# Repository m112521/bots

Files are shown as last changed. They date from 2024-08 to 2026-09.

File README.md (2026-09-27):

# BOTS

[Инструкция .PDF](https://drive.google.com/file/d/1NVx_HqoQqec8NSSLov3LOcF6pv9YKxNa/view?usp=sharing) 

[Схема .PDF](https://github.com/m112521/bots/blob/esp32-tb6612/ESP32TB6612_SVG_MOSFET/CAD/BOTS_PCB_2/BOTS_PCB_schematics.pdf)

[Исходный код](https://github.com/m112521/bots/blob/esp32-tb6612/src/web/DiffrentialControl_invert.ino) 

[BOM](https://docs.google.com/spreadsheets/d/1dyzHaP3tl7uu9WDstYaMej6k_q5ZT6EIcCH9GYrkqhs/edit?usp=sharing)

Slice 2

Slice 2 (1)

Slice 2 (2)

Slice 2 (3)

Slice 2 (4)

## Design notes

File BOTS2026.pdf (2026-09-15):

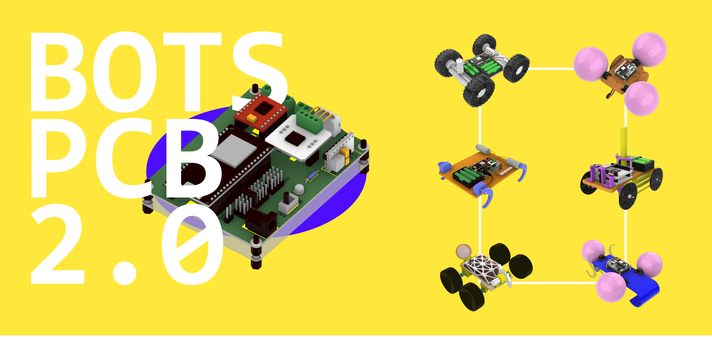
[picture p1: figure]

11 | 10 | 2 | 12
3

## 1 Плата

Набор на одну команду включает в себя:

Компоненты

1 | ESP32-WROOM 38 pin (+USB Micro)
2 | MD1 Драйвер для двух моторов TB6612
3 | T1 Силовой ключ (MOSFET) (https://amperka.ru/product/troyka-mosfet-n-channel-v3) [PIN 15]
4 | DC1 Понижающий преобразователь питания (https://amperka.ru/product/voltage-regulator-dc-dc-arduino)
5 | R1 Резистор
6 | LED1 Светодиод
7 | D1 Диод Шоттки 1N5822
8 | S1 Ползунковый переключатель
9 | P1 Гнездо питания
10 | D2 Диод 1N4001
11 | Гнездо штыревое мама
12 | M1 M2 M3 Клеммник винтовой

7

1

4

5

6

8

9

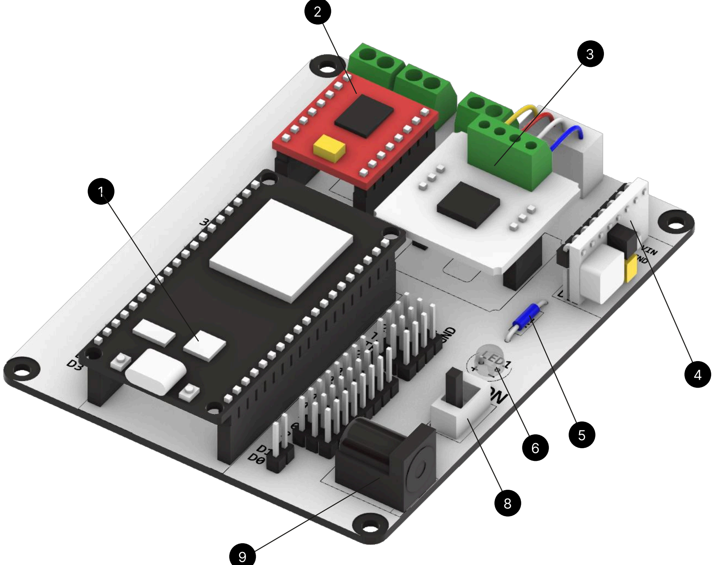
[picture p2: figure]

2 | Схема подключения питания и моторов
13 | DC-мотор 12В с редуктором (https://compacttool.ru/motor-s-reduktorom-jga25-370-12v-sootnoshenie-134-205-obmin)
14 | Держатель для 3 аккумуляторов
15 | Аккумулятор Li-ion 18650

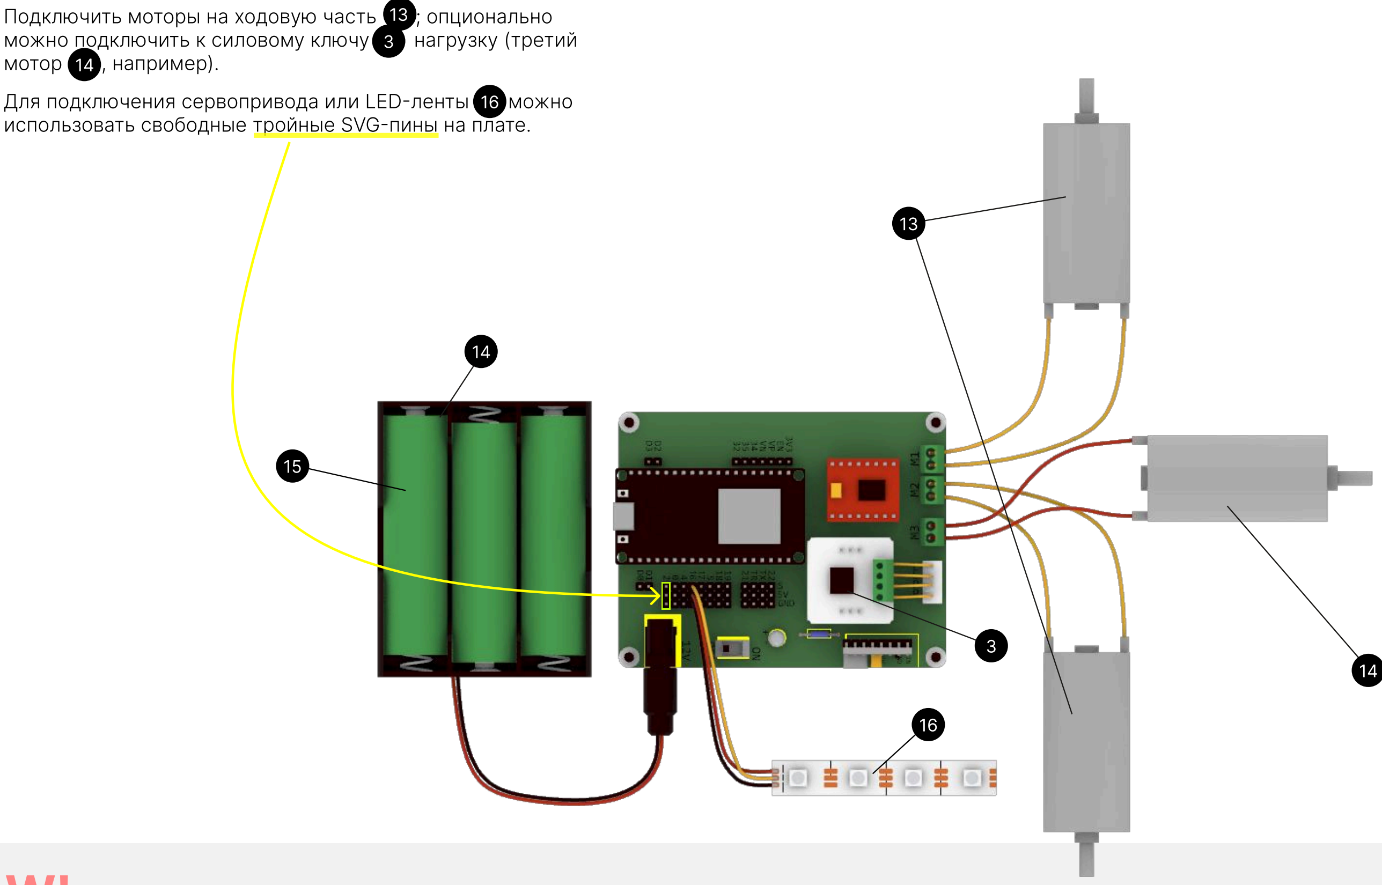
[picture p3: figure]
Подключить моторы на ходовую часть; ; опционально; можно подключить к силовому ключу; нагрузку (третий; мотор; , например).; Для подключения сервопривода или LED-ленты; можно

использовать свободные тройные SVG-пины на плате.

W! Держите заряд всех аккумуляторов выше 3.7 В

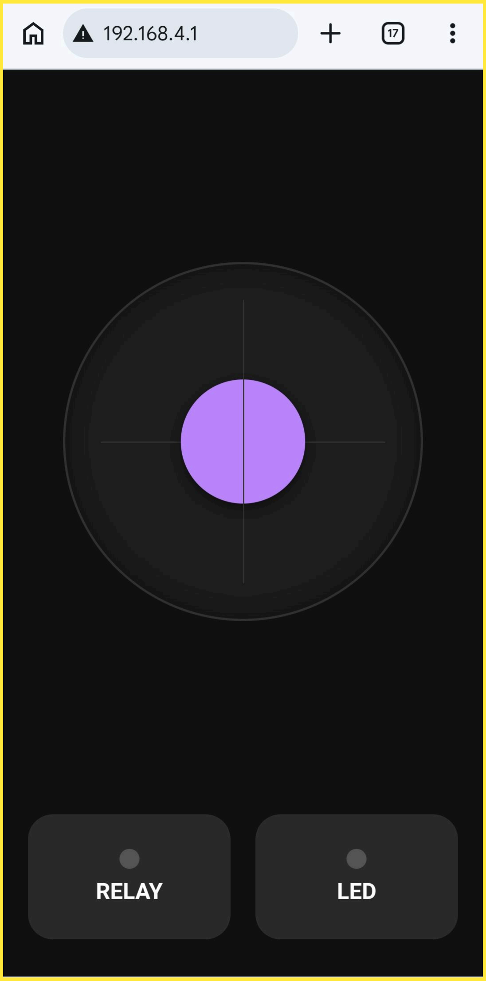
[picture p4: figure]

## 3 Управление роботом

Для управления роботом используйте смартфон:

Подключитесь к WiFi сети с именем botN (где N - номер, указанный на плате) и ввести пароль 12345678.
Откройте браузер и введите IP-адрес 192.168.4.1 в адресную строку.
Используйте джойстик для управления навпралением и скоростью движения робота.
Кнопка RELAY подает напряжение на нагрузку MOSFETа (PIN15), подключенную к клеммнику М3.

Исходный код (https://github.com/m112521/bots/blob/esp32-tb6612/src/web/DifferentialControl_AP)

## 4 Программирование (для желающих использовать свой код)

Для программирования управляющей платы понадобится скачать и установить Arduino Studio. (https://www.arduino.cc/en/software)

После запуска Arduino Studio необходимо установить дополнительные компоненты (библиотеки, плагины):

В Arduino Studio перейти в File -> Preferences. Скопировать и вставить строку ниже в поле Additional boards manager URLs (если в поле уже присутсвуют ссылки, то нужно поставить запятаю в конце строки и вставить новую ссылку):

https://espressif.github.io/arduino-esp32/package_esp32_index.json

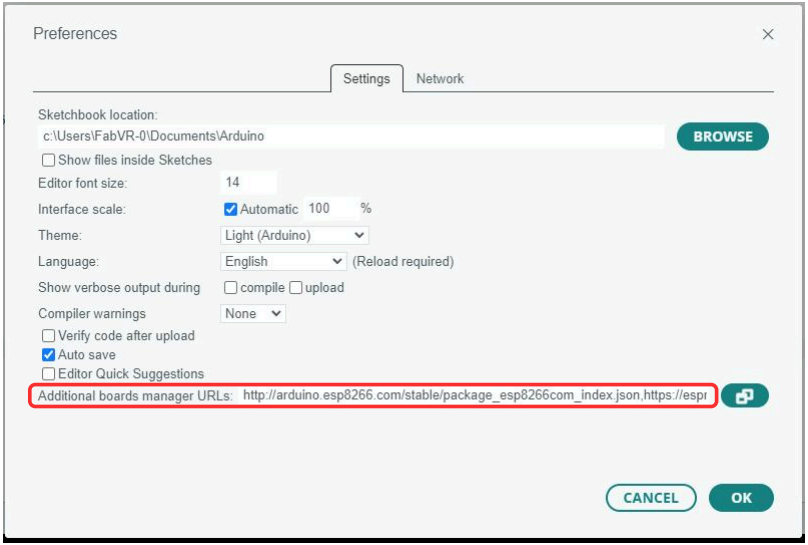
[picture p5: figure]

В Arduino Studio перейти в Boards Manager, ввести в строке поиска ESP32, найти в найденном списке esp32 by Espressif Systems , выбрать версию 2.0.15 и нажать на кнопку INSTALL : ³

1 | 2

2

2
1

3

Скачать, распаковать и установить драйвер (от имени Администратора) USB-UART CP210x_VCP_Windows.zip. (https://github.com/m112521/bots/blob/esp32-tb6612/libs/CP210x_VCP_Windows.zip)

Скачать библиотеки ниже (без раcпаковки !), перейти в Arduino Studio: Sketch -> Include Library -> Add .ZIP Library... и последовательно выбрать все скаченные архивы:

Перейти в Arduino Studio в Library Manager, ввести в поиске Arduino_JSON, найти в списке Arduino_JSON by Arduino,

выбрать версию 0.1.0 и нажать на кнопку INSTALL :

TB6612 (https://github.com/m112521/bots/blob/esp32-tb6612/libs/TB6612FNG_ESP32-master.zip)

AsyncTCP-master.zip (https://github.com/m112521/bots/blob/esp32-tb6612/libs/AsyncTCP-master.zip)

ESPAsyncWebServer-master.zi ESPAsyncWebServer-master.zi (https://github.com/m112521/bots/blob/esp32-tb6612/libs/ESPAsyncWebServer-master.zip)p (https://github.com/m112521/bots/blob/esp32-tb6612/libs/ESPAsyncWebServer-master.zip)

3

1 | 2

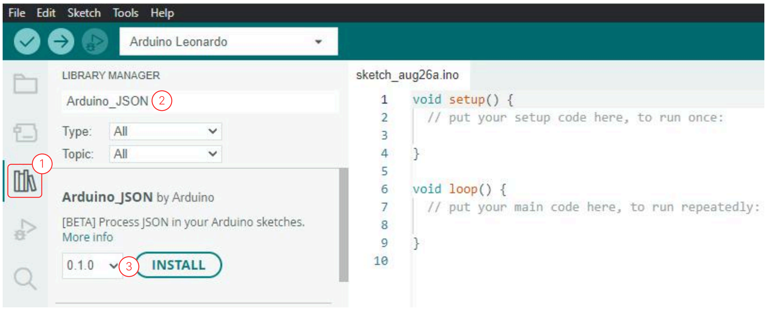
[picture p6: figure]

Перейти в Arduino Studio Library Manager, ввести в поиске AnalogWrite, найти в списке ESP32 ESP32S2 AnalogWrite by
David Lloyd, выбрать версию 5.0.1 и нажать на кнопку INSTALL : 3

1

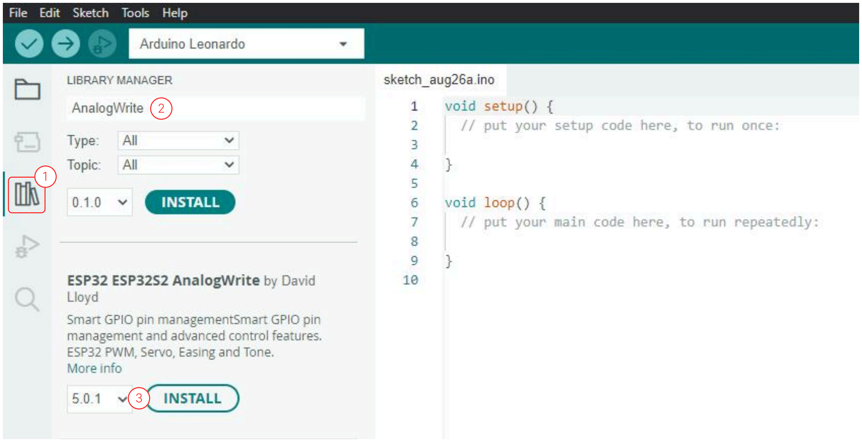
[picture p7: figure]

З агрузка новой программы. Этот пункт необходимо повторять при каждом внесении изменений в код программы:

Подключить плату ESP32 к компьютеру с помощью провода USB.

Нажать на выпающий список и выбрать USB-порт, к которому подключена управляющая плата: 1

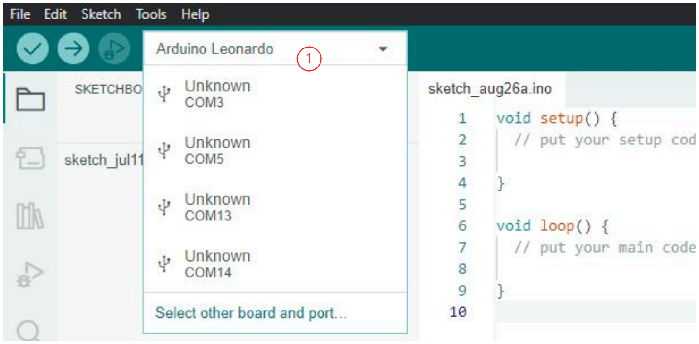
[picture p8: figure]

В строке поиска открывшегося окна ввести ESP32, выбрать из списка ESP32 Dev Module и нажать на кнопку
OK:
1 | 2

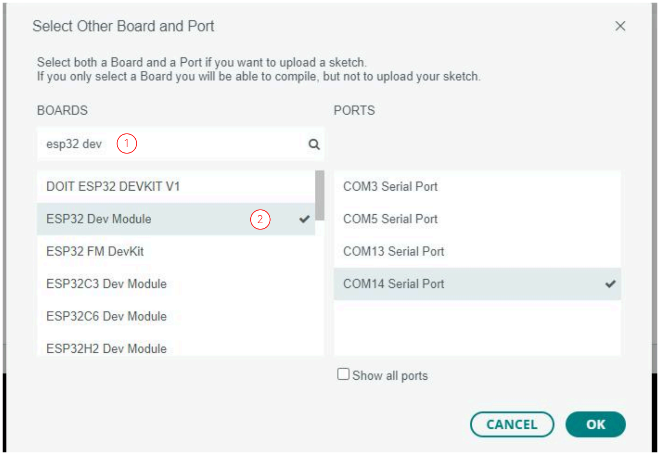
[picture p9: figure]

У бедитесь, что в поле выпадающего списка указано ESP32 Dev Module. После нажмите на кнопку | для
загрузки программы на микроконтроллер:
1 | 2
2 | 1

Во врямя загрузки программы (до появления сообщения об успешной загрузке в Arduino Studio) необходимо удерживать кнопку BOOT на управляющей плате: ¹

После успешной загрузки кода необходимо перезагрузить плату, нажав на кнопку RST.

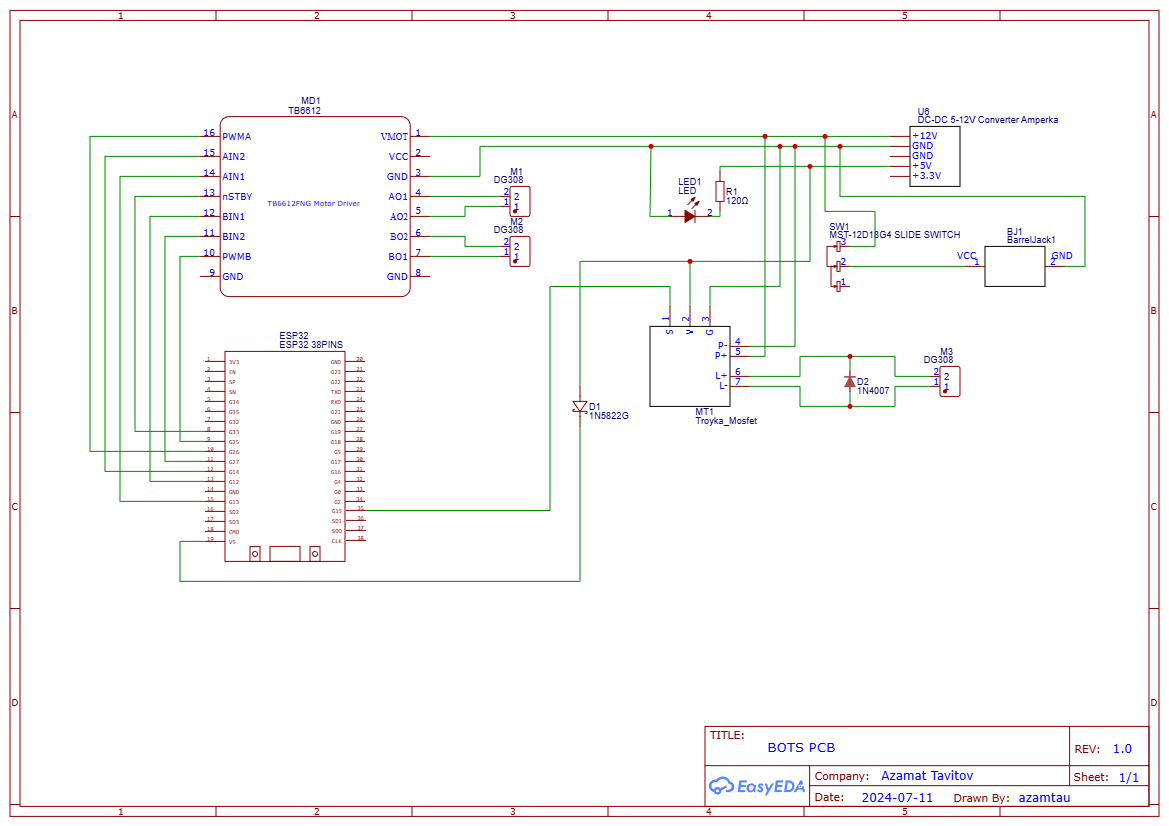
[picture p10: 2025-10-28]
ESP32TB6612_SVG_MOSFET/CAD/BOTS_PCB_2/Schematic_tb6612esp32_2025-10-28.png

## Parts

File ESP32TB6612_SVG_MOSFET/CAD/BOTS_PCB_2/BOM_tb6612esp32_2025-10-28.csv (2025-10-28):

ID | Name | Designator | Footprint | Quantity | Manufacturer Part | Manufacturer | Supplier | Supplier Part | Price | Pins
1 | BarrelJack1 | BJ1 | BARRELJACKFC681478 | 1 |  |  |  |  |  | 2
2 | 1N5822G | D1 | DO-201AD_BD5.1-L8.4-P12.50-D1.3-FD-1 | 1 | 1N5822G | onsemi(安森美) | LCSC | C59208 | 0.589 | 2
3 | 1N4007 | D2 | 1N4007 | 1 |  |  |  |  |  | 2
4 | ESP32 38PINS | ESP32 | ESP32 38PINS | 1 |  |  |  |  |  | 38
5 | LED | LED1 | LED-TH_LED-DP2-2LED-AMCC | 1 | 5600 | VccLite | Digi-Key | L20325-ND |  | 2
6 | DG308 | M1,M2,M3 | CONN-TH_DG308-2.54-02P-14-00A | 3 | DG308-2.54-02P-14-00A(H) | DEGSON（高正/高松） | LCSC | C699496 | 0.312 | 2
7 | TB6612 | MD1 | TB6612FNG | 1 |  |  |  |  |  | 16
8 | Troyka_Mosfet | MT1 | TROYKA MOSFET | 1 |  | Amperka |  |  |  | 7
9 | 120Ω | R1 | RES-TH_BD2.3-L6.5-P10.50-D0.5 | 1 | CF1/4W-110KΩ±5% T52 | CCO(千志电子) | LCSC | C120104 | 0.006 | 2
10 | MST-12D18G4 SLIDE SWITCH | SW1 | SW-SMD_MST-12D18G4-SPDT-SLIDE-SWITCH | 1 | MST-12D18G4 SPDT Slide Switch | SHOU HAN(首韩) | LCSC | C49023767 | 0.075 | 3
11 | DC-DC 5-12V Converter Amperka | U6 | DC-DC 5-12V CONVERTER AMPERKA | 1 | DC-DC Converter |  |  |  |  | 5

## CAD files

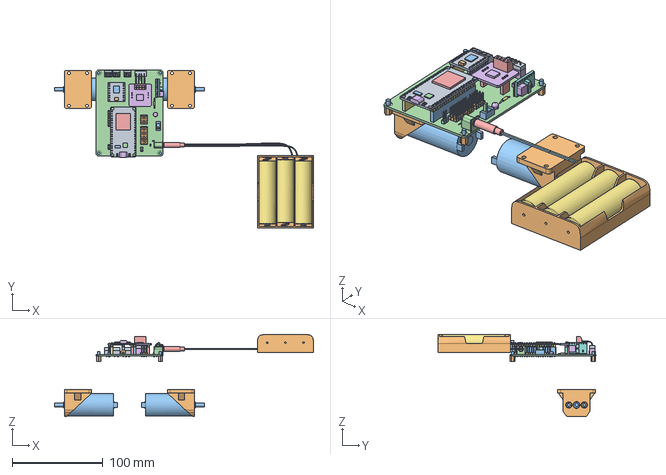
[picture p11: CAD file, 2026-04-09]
Electronics_Assembly_PCB2.stp
286.2 x 174.5 x 91.1 mm

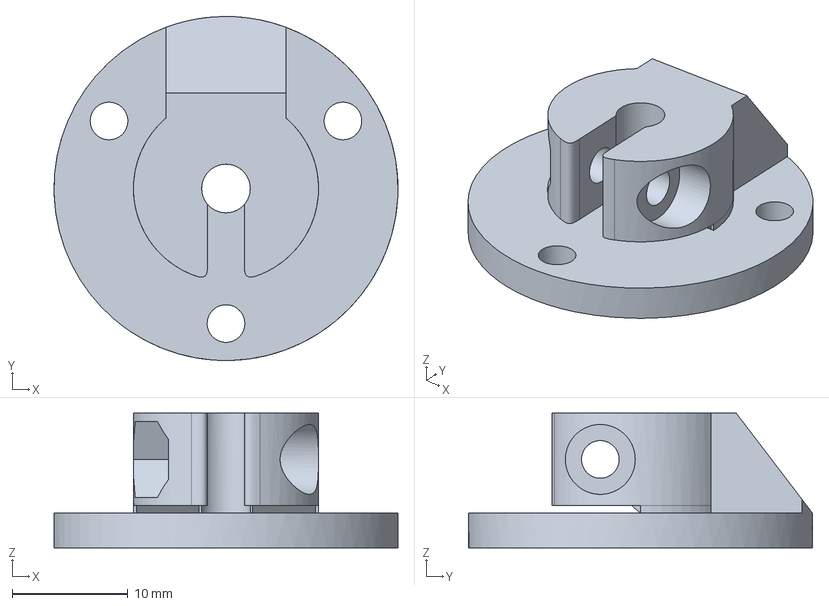
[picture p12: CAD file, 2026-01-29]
BOTS_BOX/onShaftHolder.stp
29.7 x 29.7 x 11.6 mm

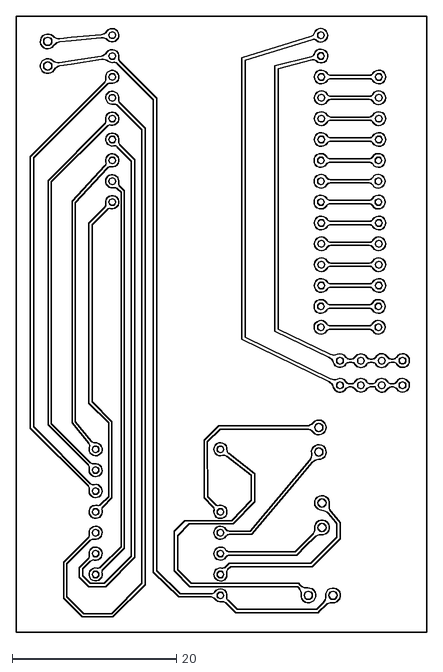
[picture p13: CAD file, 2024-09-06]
ESP32TB6612_SVG/ESP8266TB6612_SVG_ENC_SeparatedPower.dxf
50.0 x 75.0

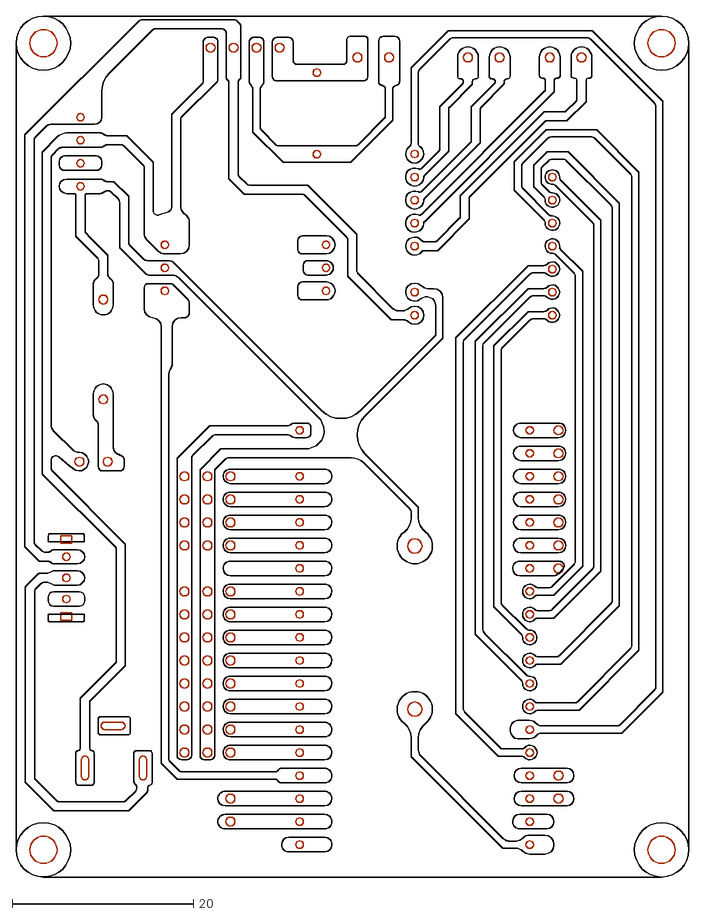
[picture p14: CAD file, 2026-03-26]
ESP32TB6612_SVG_MOSFET/CAD/BOTS_PCB_2/BOTS_PCB_2.2_TRACES_MIRROR.dxf
74.2 x 95.0

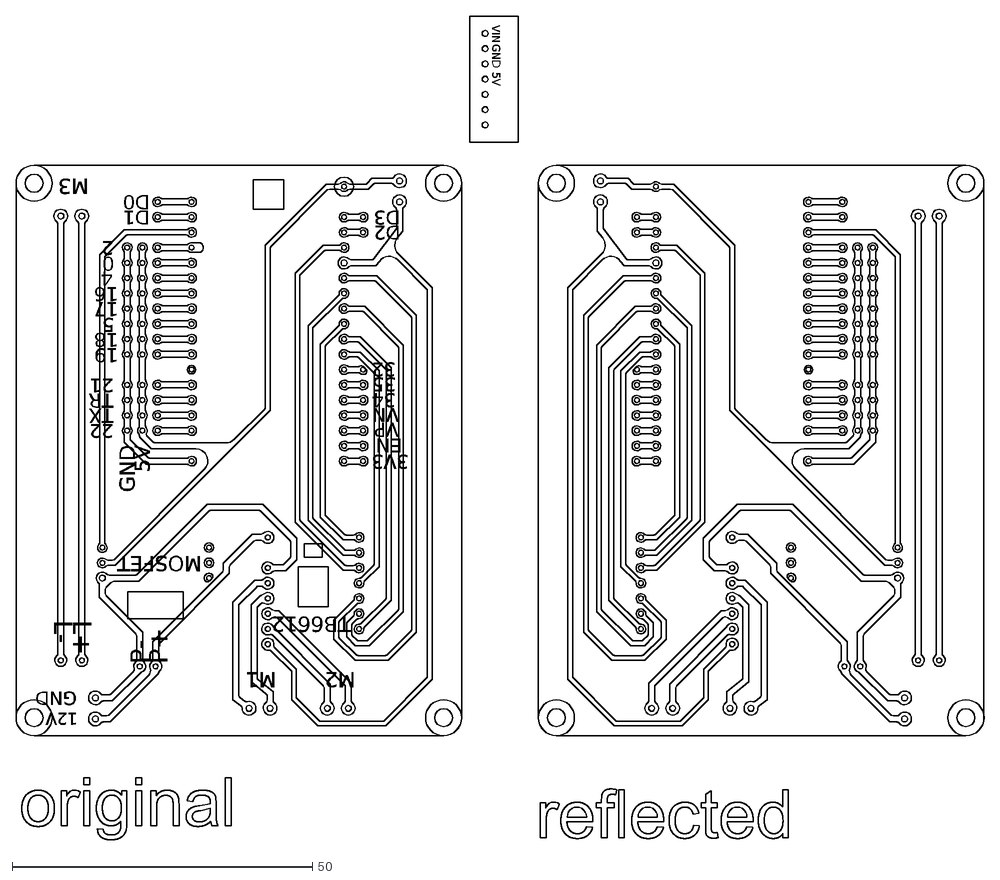
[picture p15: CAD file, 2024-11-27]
ESP32TB6612_SVG_MOSFET/CAD/ESP32TB6612_MOSFET_vector.dxf
5V
GND
VIN
P-
12V
L-
L+
P+
MOSFET
D2
D3
D0
D1
19
18
5
17
2
4
16
0
21
TR
TX
22
32
35
34
VN
VP
EN
3V3
TB6612
M3
M1
M2

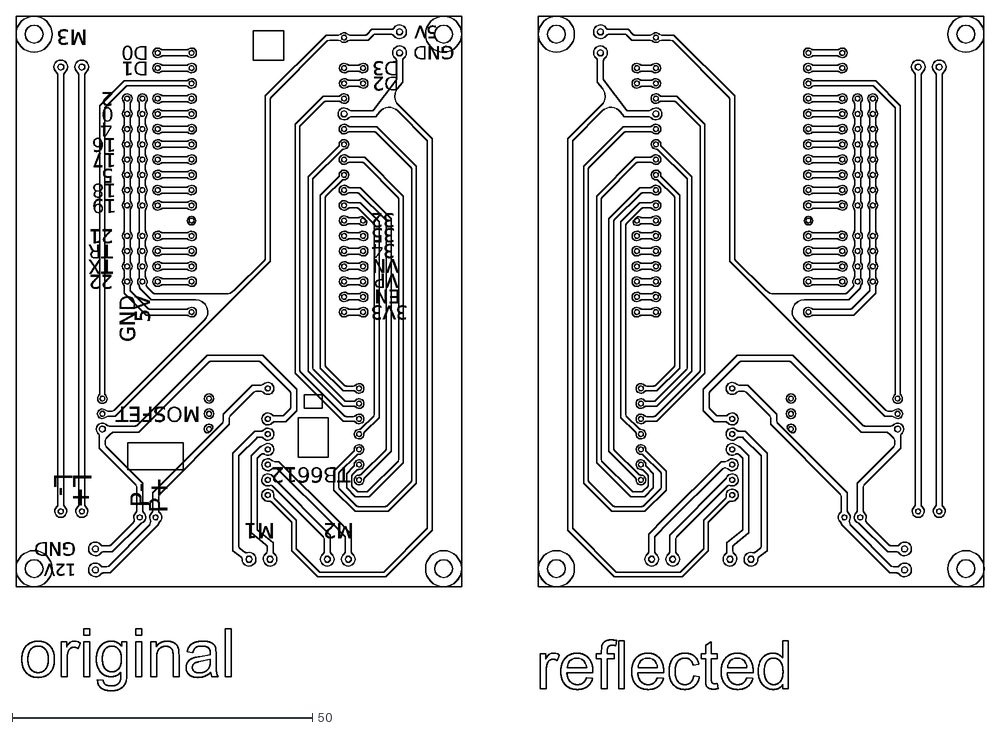
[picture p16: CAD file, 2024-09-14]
ESP32TB6612_SVG_MOSFET/CAM/250x150/ESP32TB6612_MOSFET_vector.dxf
5V
M2
M1
M3
GND
TB6612
3V3
EN
VP
VN
34
35
32
22
TX
TR
21
0
16
4
2
17
5
18
19
D1
D0
D3
D2
MOSFET
P+
P-
L+
L-
12V

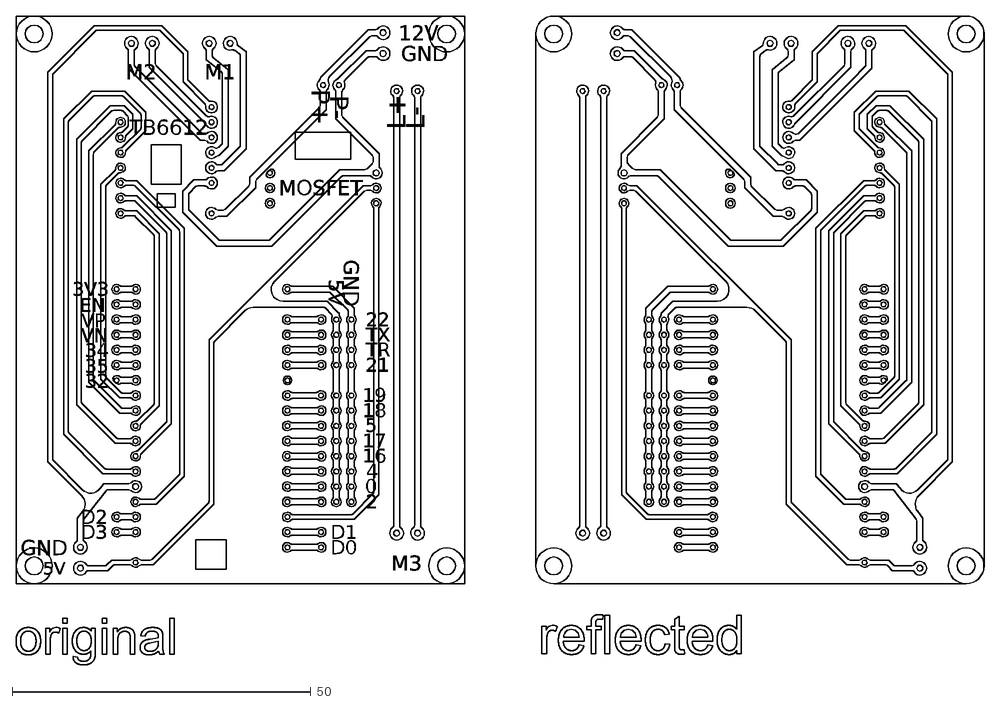
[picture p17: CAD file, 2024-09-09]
ESP32TB6612_SVG_MOSFET/CAM/ESP32TB6612_MOSFET_vector.dxf
L-
L+
P-
P+
MOSFET
D2
D3
D0
D1
19
18
5
17
2
4
16
0
21
TR
TX
22
32
35
34
VN
VP
EN
3V3
5V
TB6612
GND
M3
M1
M2
12V

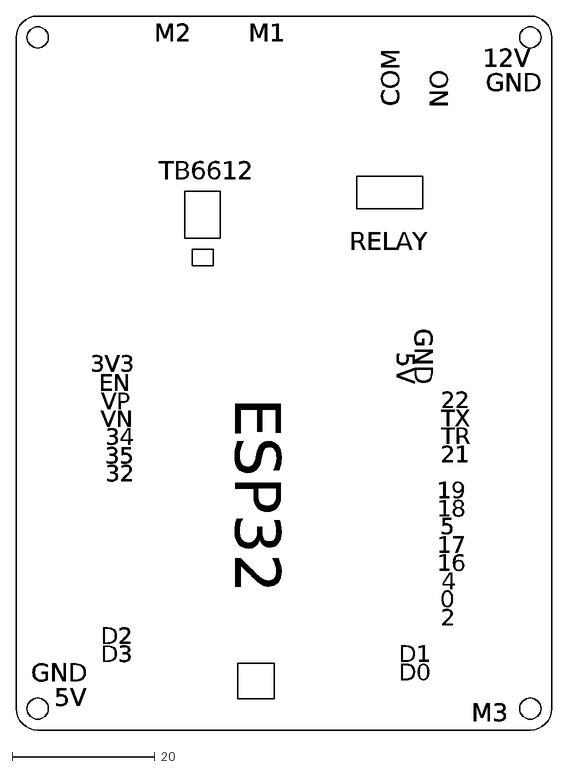
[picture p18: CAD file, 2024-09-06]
ESP32TB6612_SVG_RELAY/CAD/SilkBOTS-Shield.dxf
ESP32
GND
12V
D2
D3
D0
D1
19
18
5
17
2
4
16
0
21
TR
TX
22
32
35
34
VN
VP
EN
3V3
5V
M2
M1
M3
TB6612
RELAY
COM
NO

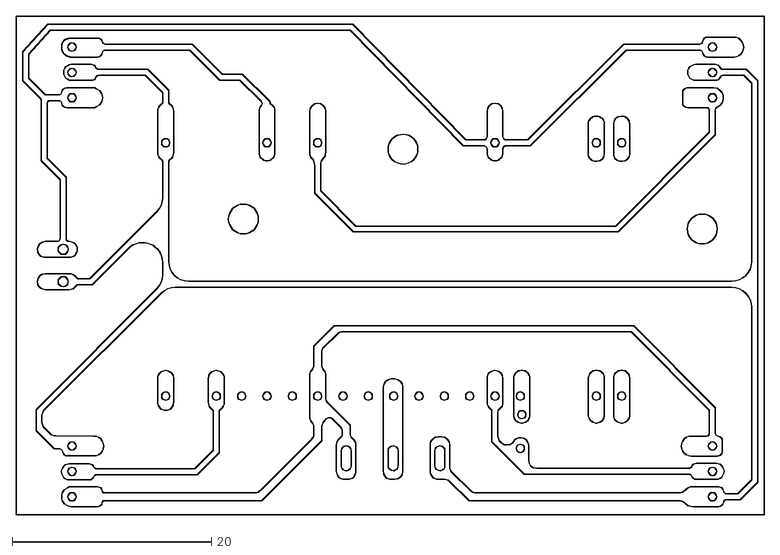
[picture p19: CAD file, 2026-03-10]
ESPNOW_JOYSTICK/CAD/minibot_traces_R12Lines.dxf
75.0 x 50.0

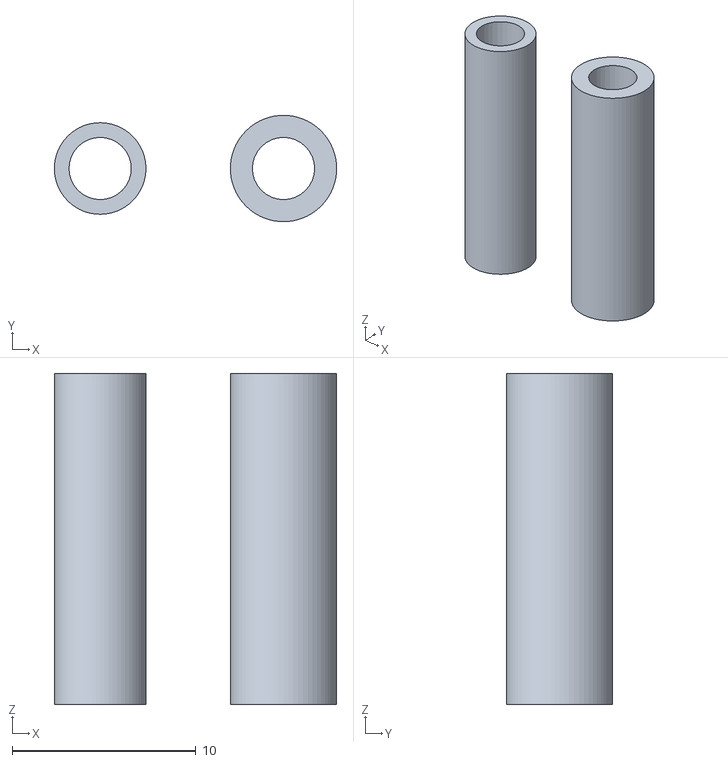
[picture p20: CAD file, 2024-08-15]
ESPNOW_JOYSTICK/STL/spacersJoystick.stl
15.4 x 5.78 x 18.0

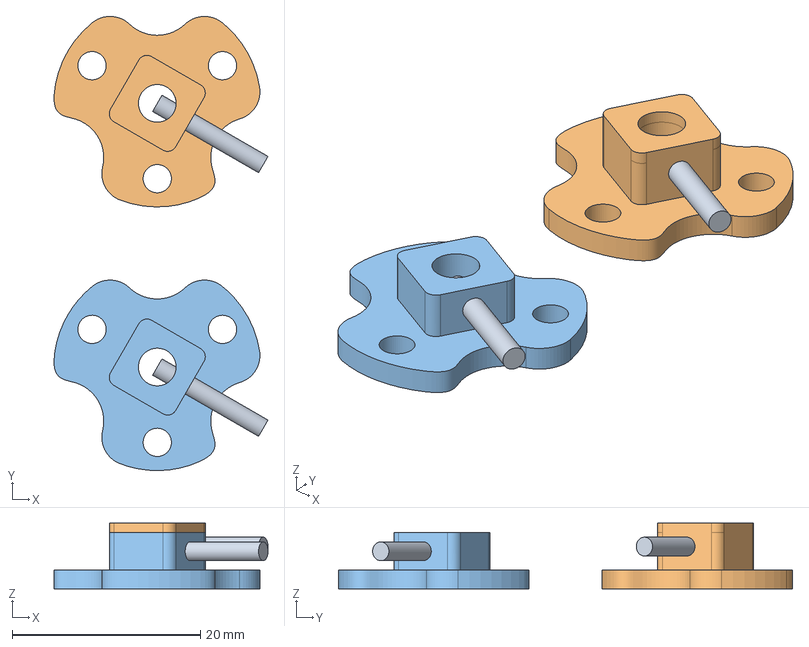
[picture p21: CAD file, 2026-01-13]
BOTS_BOX/onShaftHolder_cnc.stp
22.7 x 48.2 x 7.00 mm

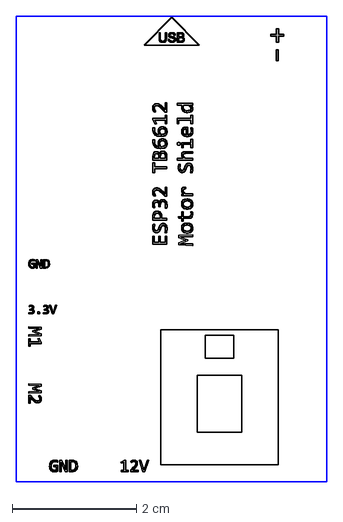
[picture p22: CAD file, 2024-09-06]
ESP32TB6612_SVG/ESP8266TB6612_SVG_ENC_SeparatedPower_silk.dxf
5.00 x 7.50 cm

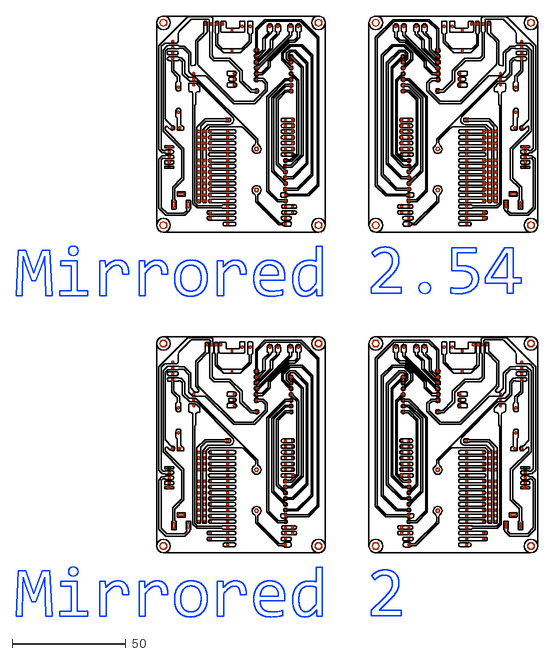
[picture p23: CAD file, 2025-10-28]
ESP32TB6612_SVG_MOSFET/CAD/BOTS_PCB_2/BOTS_PCB_2.0_TRACES_HOLES.dxf
229.3 x 264.2

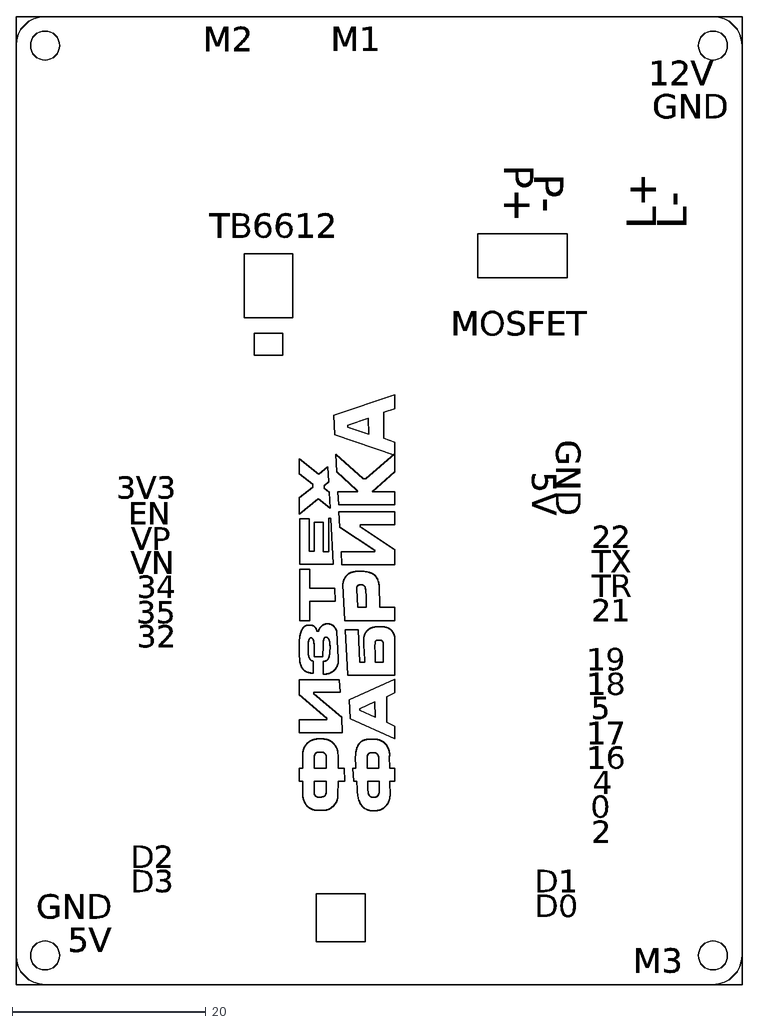
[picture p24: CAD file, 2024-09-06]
ESP32TB6612_SVG_MOSFET/CAD/ESP32TB6612_MOSFET_SILK_FF.dxf
GND
TB6612
5V
M3
M1
M2
3V3
EN
VP
VN
34
35
32
22
TX
TR
21
0
16
4
2
17
5
18
19
D1
D0
D3
D2
12V
MOSFET
P+
P-
L+
L-

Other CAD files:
ESPNOW_JOYSTICK/CAD/minibot_traces_R12Natural.dxf
BOTS_BOX/bots_cb_box.dxf
ESP32TB6612_SVG_MOSFET/CAD/BOTS_PCB_2/UVMaskForRhino.dxf
ESP32TB6612_SVG_MOSFET/CAD/ESP32TB6612_MOSFET_TRACES.dxf
BOTS_BOX/cap.stl
BOTS_BOX/cap_acrylic.dxf
BOTS_BOX/cap_aracal.dxf
BOTS_BOX/cap_graph.dxf
BOTS_BOX/clamp.stl
BOTS_BOX/holderFootprint.dxf
BOTS_BOX/level3.stl
BOTS_BOX/onoffFootprint.dxf
BOTS_BOX/shell.stl
ESP32TB6612_SVG/ESP32TB6612_SVG.3dm
ESP32TB6612_SVG_MOSFET/CAD/BOTS_PCB_2.0.3dm
ESP32TB6612_SVG_MOSFET/CAD/BOTS_PCB_2/BOTS2_Engraving.dxf
ESP32TB6612_SVG_MOSFET/CAD/BOTS_PCB_2/BOTS2_TracesOnly.dxf
ESP32TB6612_SVG_MOSFET/CAD/BOTS_PCB_2/BOTS_PCB_2.0_R7.3dm
ESP32TB6612_SVG_MOSFET/CAD/BOTS_PCB_2/BOTS_PCB_2_Mask.dxf
ESP32TB6612_SVG_MOSFET/CAD/BOTS_PCB_2/ServoShileld.dxf
ESP32TB6612_SVG_MOSFET/CAD/ESP32TB6612_MOSFET_SILK.dxf
ESP32TB6612_SVG_MOSFET/CAD/ESP32TB6612_MOSFET_TRACES_FF.dxf
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

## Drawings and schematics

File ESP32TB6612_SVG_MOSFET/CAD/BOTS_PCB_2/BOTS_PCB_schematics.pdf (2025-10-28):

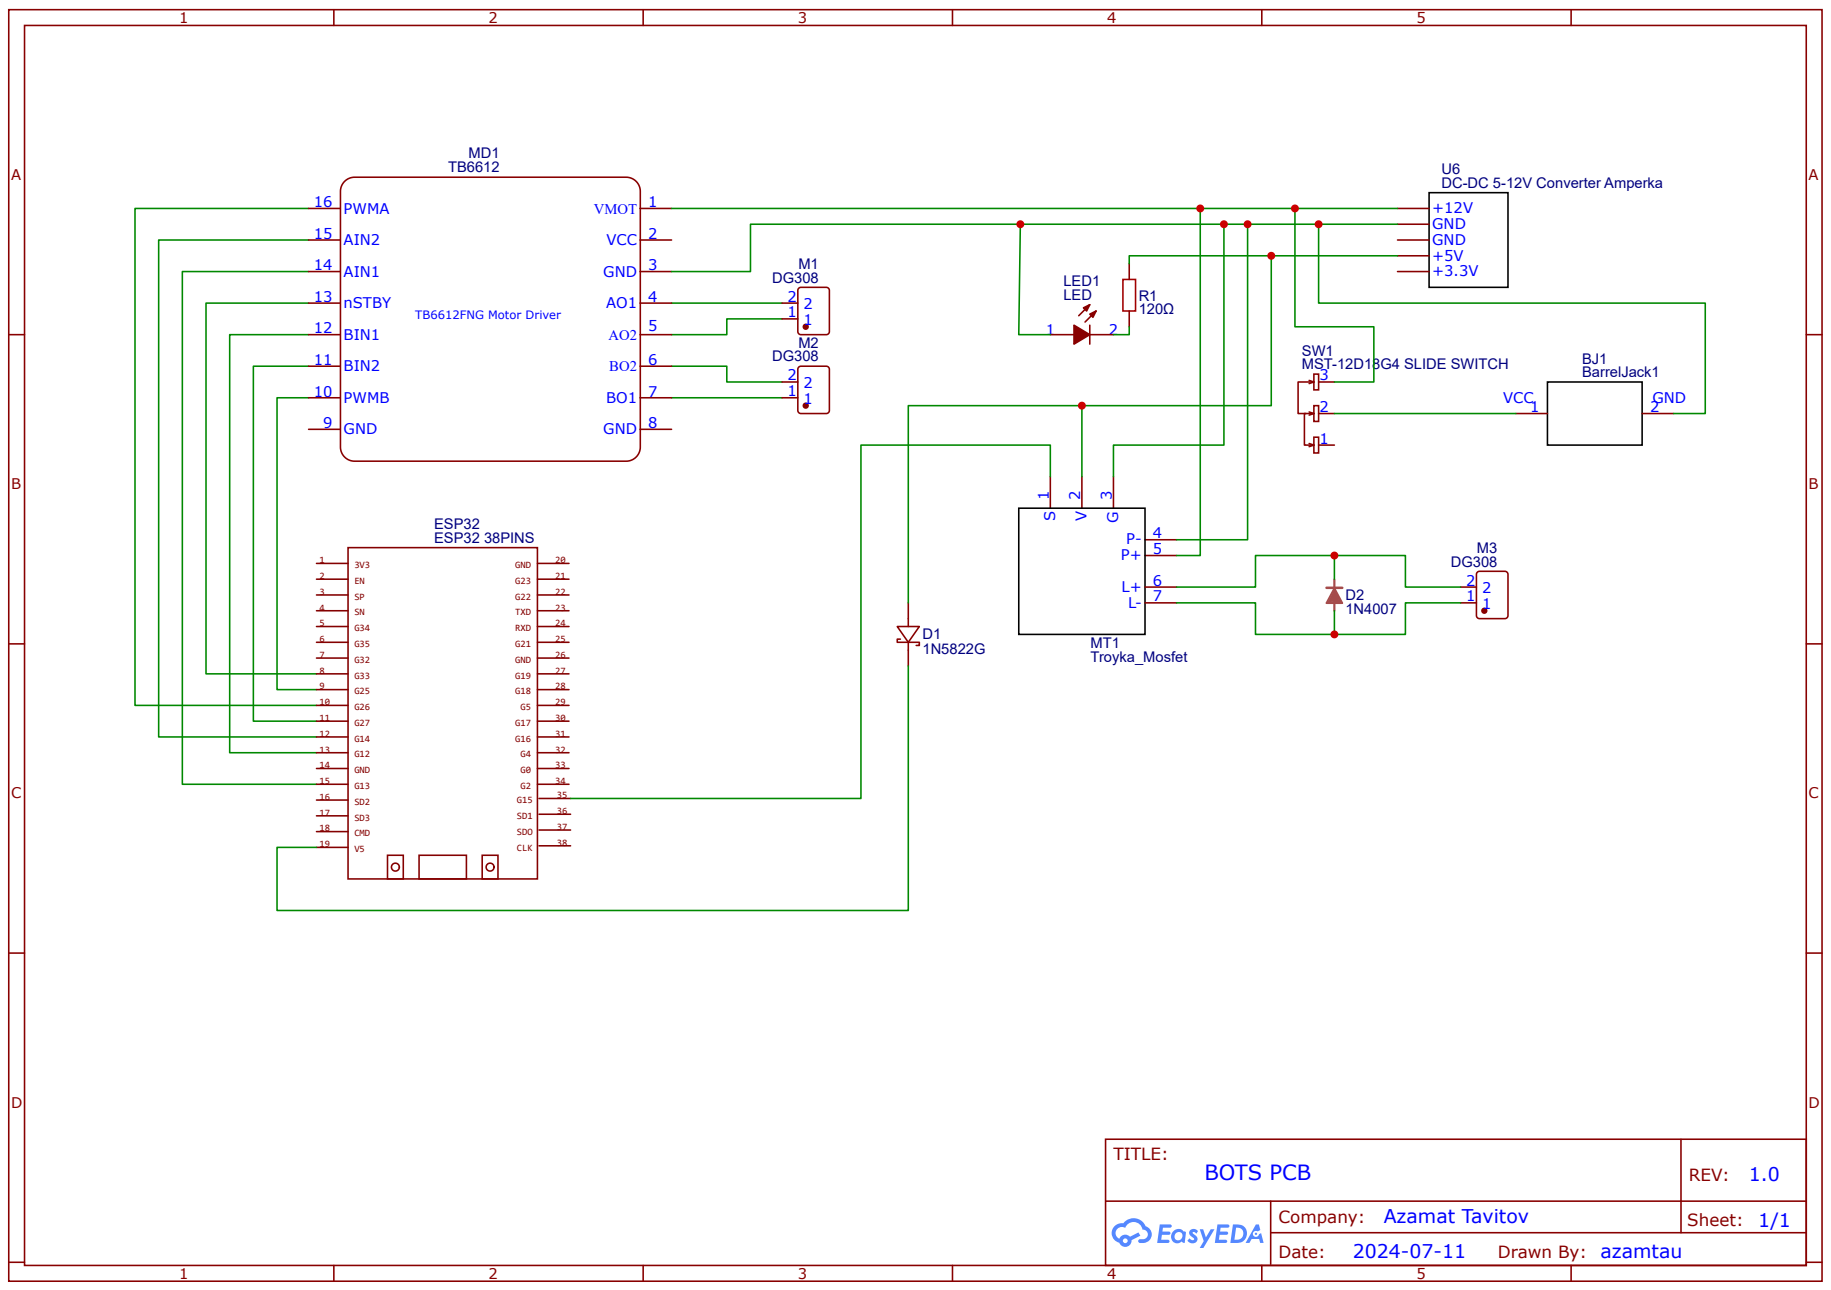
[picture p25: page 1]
TITLE:; BOTS PCB; REV: 1.0; Date:; Sheet: 1/1; VMOT 1; VCC; GND; 8 GND; PWMB 10; BIN2; BIN1; nSTBY 13; AIN1; AIN2; PWMA 16; TB6612FNG Motor Driver; ESP32 38PINS; ESP32; TXD; RXD; CLK; SDO; CMD; Troyka_Mosfet; DC-DC 5-12V Converter Amperka; MST-12D18G4 SLIDE SWITCH; BarrelJack1; VCC 1; GND 2; LED; LED1

Company: Azamat Tavitov

Drawn By: azamtau

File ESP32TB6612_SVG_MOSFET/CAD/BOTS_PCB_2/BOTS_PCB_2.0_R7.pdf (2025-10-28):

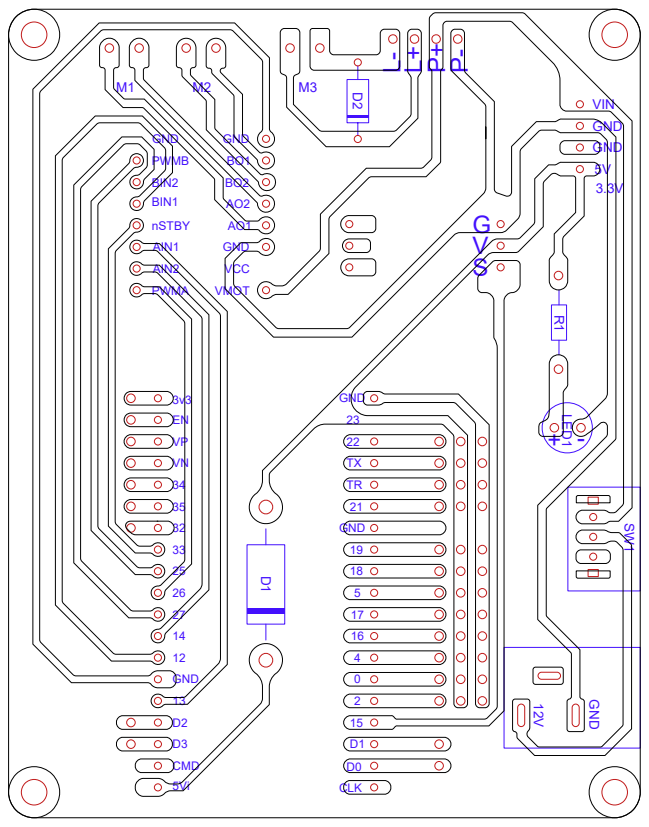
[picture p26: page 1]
GND; LED1; PWMA; CMD; VIN; BIN2; BIN1; nSTBY; AIN1; VCC; AIN2; CLK; PWMB

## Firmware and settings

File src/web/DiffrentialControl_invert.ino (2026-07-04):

#include <TB6612_ESP32.h>
#include <WiFi.h>
#include <AsyncTCP.h>
#include <ESPAsyncWebServer.h>
#include <Arduino_JSON.h>

#define AIN1 13
#define BIN1 12
#define AIN2 14
#define BIN2 27
#define PWMA 26
#define PWMB 25
#define STBY 33

const char* ssid = "bot1";
const char* password = "12345678";

#define RELAY_PIN 15
#define LED_PIN 2 

// Replaced 'direction' and 'speed' with X/Y coordinates
int joyX = 0; 
int joyY = 0;
int fire = 0;
int led = 0;

// Motor inversion states (1 = normal, -1 = inverted)
int invert1 = 1;
int invert2 = 1;

unsigned long lastCommandTime = 0; 
const long COMMAND_TIMEOUT = 3000; 

AsyncWebServer server(80);
AsyncWebSocket ws("/ws");

JSONVar readings;

const int offsetA = 1;
const int offsetB = 1;

Motor motor1 = Motor(AIN1, AIN2, PWMA, offsetA, STBY, 5000, 8, 1);
Motor motor2 = Motor(BIN1, BIN2, PWMB, offsetB, STBY, 5000, 8, 2);

const char index_html[] PROGMEM = R"rawliteral(
<!DOCTYPE html>
<html>
<head>
    <meta name="viewport" content="width=device-width, initial-scale=1.0, maximum-scale=1.0, user-scalable=no">
    <title>Bot Controller</title>
    <style>
        :root {
            --bg-color: #121212;
            --card-bg: #1e1e1e;
            --text-color: #ffffff;
            --btn-bg: #2c2c2c;
            --accent: #bb86fc;
            --fire-color: #cf6679;
            --led-color: #03dac6;
            --invert-color: #ffb74b; /* Orange for invert buttons */
        }

        * { box-sizing: border-box; margin: 0; padding: 0; }

        body {
            background-color: var(--bg-color);
            color: var(--text-color);
            font-family: -apple-system, BlinkMacSystemFont, "Segoe UI", Roboto, Helvetica, Arial, sans-serif;
            height: 100dvh;
            width: 100vw;
            overflow: hidden;
            display: flex;
            justify-content: center;
            align-items: center;
            -webkit-user-select: none;
            user-select: none;
            touch-action: none; 
        }

        .controller {
            display: flex;
            flex-direction: column;
            width: 100%;
            max-width: 500px;
            height: 100%;
            padding: 20px;
            gap: 20px;
        }

        /* --- JOYSTICK SECTION --- */
        .joystick-section {
            flex: 1; /* Takes up all remaining space */
            display: flex;
            justify-content: center;
            align-items: center;
            min-height: 0;
        }

        .joystick-zone {
            position: relative;
            width: min(75vw, 350px);
            aspect-ratio: 1 / 1; /* Perfect circle */
            max-height: 100%;
            background-color: var(--card-bg);
            border-radius: 50%;
            border: 2px solid #333;
            box-shadow: inset 0 0 20px rgba(0,0,0,0.5);
        }

        /* Crosshair in the center for visual reference */
        .joystick-zone::before, .joystick-zone::after {
            content: '';
            position: absolute;
            background: #333;
        }
        .joystick-zone::before { top: 50%; left: 10%; right: 10%; height: 1px; }
        .joystick-zone::after { left: 50%; top: 10%; bottom: 10%; width: 1px; }

        .joystick-knob {
            position: absolute;
            width: 35%;
            height: 35%;
            background-color: var(--accent);
            border-radius: 50%;
            top: 50%;
            left: 50%;
            transform: translate(-50%, -50%); /* Center it perfectly */
            box-shadow: 0 4px 10px rgba(0,0,0,0.5);
            pointer-events: none; /* Touches go to the zone, not the knob */
            transition: box-shadow 0.2s;
        }

        .joystick-knob.active {
            box-shadow: 0 0 20px var(--accent);
        }

        /* --- ACTION SECTION --- */
        .action-section {
            flex: 0 0 auto;
            display: grid;
            grid-template-columns: 1fr 1fr; /* 2x2 Grid layout */
            gap: 15px;
            padding-bottom: 10px;
        }

        .action-btn {
            width: 100%;
            aspect-ratio: 2.2 / 1; /* Wider buttons for the grid */
            max-height: 90px;
            background-color: var(--btn-bg);
            border: 3px solid transparent;
            border-radius: 20px;
            color: var(--text-color);
            font-size: 16px;
            font-weight: bold;
            display: flex;
            flex-direction: column;
            justify-content: center;
            align-items: center;
            gap: 6px;
            outline: none;
            -webkit-tap-highlight-color: transparent;
            transition: all 0.2s;
        }

        .indicator {
            width: 14px;
            height: 14px;
            border-radius: 50%;
            background-color: #555;
            transition: background-color 0.2s;
        }

        .fire-active { border-color: var(--fire-color); }
        .fire-active .indicator { background-color: var(--fire-color); box-shadow: 0 0 10px var(--fire-color); }

        .led-active { border-color: var(--led-color); }
        .led-active .indicator { background-color: var(--led-color); box-shadow: 0 0 10px var(--led-color); }

        .invert-active { border-color: var(--invert-color); }
        .invert-active .indicator { background-color: var(--invert-color); box-shadow: 0 0 10px var(--invert-color); }

    </style>
</head>
<body>

    <div class="controller">
        <!-- Joystick -->
        <div class="joystick-section">
            <div class="joystick-zone" id="joystick-zone">
                <div class="joystick-knob" id="joystick-knob"></div>
            </div>
        </div>

        <!-- Action Buttons (2x2 Grid) -->
        <div class="action-section">
            <button class="action-btn" id="btn-fire">
                <div class="indicator"></div>
                RELAY
            </button>
            <button class="action-btn" id="btn-led">
                <div class="indicator"></div>
                LED
            </button>
            <button class="action-btn" id="btn-invert1">
                <div class="indicator"></div>
                INVERT M1
            </button>
            <button class="action-btn" id="btn-invert2">
                <div class="indicator"></div>
                INVERT M2
            </button>
        </div>
    </div>

<script>
let gateway = `ws://${window.location.hostname}/ws`;
let websocket;

const zone = document.getElementById('joystick-zone');
const knob = document.getElementById('joystick-knob');
let isDragging = false;
let zoneRect, maxRadius;

window.addEventListener('load', onload);

function onload(event) {
    initWebSocket();
    initButtons();
    initJoystick();
}

function initJoystick() {
    // Recalculate dimensions in case of screen rotation
    function updateDimensions() {
        zoneRect = zone.getBoundingClientRect();
        maxRadius = zoneRect.width / 2;
    }
    updateDimensions();
    window.addEventListener('resize', updateDimensions);

    function handleMove(clientX, clientY) {
        let dx = clientX - (zoneRect.left + maxRadius);
        let dy = clientY - (zoneRect.top + maxRadius);
        
        const distance = Math.min(Math.sqrt(dx*dx + dy*dy), maxRadius);
        const angle = Math.atan2(dy, dx);
        
        // Calculate clamped X and Y for the visual knob
        const clampedX = distance * Math.cos(angle);
        const clampedY = distance * Math.sin(angle);
        
        knob.style.transform = `translate(calc(-50% + ${clampedX}px), calc(-50% + ${clampedY}px))`;

        // Map to -255 to 255. Y is inverted (up is positive)
        const outX = Math.round((clampedX / maxRadius) * 255);
        const outY = Math.round((-clampedY / maxRadius) * 255); 

        if(websocket && websocket.readyState === WebSocket.OPEN){
            websocket.send(JSON.stringify({x: outX, y: outY}));
        }
    }

    function endMove() {
        isDragging = false;
        knob.style.transform = `translate(-50%, -50%)`;
        knob.classList.remove('active');
        if(websocket && websocket.readyState === WebSocket.OPEN){
            websocket.send(JSON.stringify({x: 0, y: 0}));
        }
    }

    // Touch Events
    zone.addEventListener('touchstart', (e) => {
        e.preventDefault();
        isDragging = true;
        zoneRect = zone.getBoundingClientRect(); // Update on press
        knob.classList.add('active');
        handleMove(e.touches[0].clientX, e.touches[0].clientY);
    });

    zone.addEventListener('touchmove', (e) => {
        e.preventDefault();
        if(isDragging) handleMove(e.touches[0].clientX, e.touches[0].clientY);
    });

    zone.addEventListener('touchend', (e) => {
        e.preventDefault();
        endMove();
    });

    zone.addEventListener('touchcancel', (e) => {
        e.preventDefault();
        endMove();
    });
}

function initButtons() {
  document.querySelector('#btn-led').addEventListener('click', ()=>{ 
    let btn = document.querySelector('#btn-led');
    btn.classList.toggle('led-active');
    let state = btn.classList.contains('led-active') ? 1 : 0;
    websocket.send(JSON.stringify({led: state})); 
  });
  
  document.querySelector('#btn-fire').addEventListener('click', ()=>{ 
    let btn = document.querySelector('#btn-fire');
    btn.classList.toggle('fire-active');
    let state = btn.classList.contains('fire-active') ? 1 : 0;
    websocket.send(JSON.stringify({fire: state})); 
  });

  document.querySelector('#btn-invert1').addEventListener('click', ()=>{ 
    let btn = document.querySelector('#btn-invert1');
    btn.classList.toggle('invert-active');
    let state = btn.classList.contains('invert-active') ? 1 : 0;
    websocket.send(JSON.stringify({invert1: state})); 
  });

  document.querySelector('#btn-invert2').addEventListener('click', ()=>{ 
    let btn = document.querySelector('#btn-invert2');
    btn.classList.toggle('invert-active');
    let state = btn.classList.contains('invert-active') ? 1 : 0;
    websocket.send(JSON.stringify({invert2: state})); 
  });
}

function initWebSocket() {
    console.log('Trying to open a WebSocket connection…');
    websocket = new WebSocket(gateway);
    websocket.onopen = onOpen;
    websocket.onclose = onClose;
}

function onOpen(event) {
    console.log('Connection opened');
}

function onClose(event) {
    console.log('Connection closed');
    setTimeout(initWebSocket, 2000);
}
</script>
</body>
</html>
)rawliteral";


void initWiFi() {
  WiFi.mode(WIFI_AP);
  WiFi.softAP(ssid, password);
  Serial.print("Access Point started. Connect to WiFi: ");
  Serial.println(ssid);
  Serial.print("AP IP address: ");
  Serial.println(WiFi.softAPIP());
}

void handleWebSocketMessage(void *arg, uint8_t *data, size_t len) {
  AwsFrameInfo *info = (AwsFrameInfo*)arg;
  if (info->final && info->index == 0 && info->len == len && info->opcode == WS_TEXT) {
    
    lastCommandTime = millis(); 

    JSONVar myObject = JSON.parse((const char*)data);

    // Handle Joystick X and Y data
    if (myObject.hasOwnProperty("x") && myObject.hasOwnProperty("y")) {
      joyX = (int)myObject["x"];
      joyY = (int)myObject["y"];
      driveMix(joyX, joyY);
    }
    else if (myObject.hasOwnProperty("fire")) {
      fire = (int)myObject["fire"];      
    }
    else if (myObject.hasOwnProperty("led")) {
      led = (int)myObject["led"];      
    }
    else if (myObject.hasOwnProperty("invert1")) {
      // If 1 is received, set to -1 (invert). If 0, set to 1 (normal)
      invert1 = ((int)myObject["invert1"] == 1) ? -1 : 1;      
    }
    else if (myObject.hasOwnProperty("invert2")) {
      invert2 = ((int)myObject["invert2"] == 1) ? -1 : 1;      
    }
  }
}

// Differential Drive Mixer
// Converts X (turning) and Y (throttle) into Left/Right motor speeds
void driveMix(int x, int y) {
  // Calculate raw motor outputs and apply inversion multipliers
  int leftMotor  = (y + x) * invert1;
  int rightMotor = (y - x) * invert2;

  // Constrain values to -255 to 255
  leftMotor  = constrain(leftMotor,  -255, 255);
  rightMotor = constrain(rightMotor, -255, 255);

  // Apply to motors (positive = forward, negative = backward based on offset)
  if (leftMotor == 0 && rightMotor == 0) {
    motor1.brake();
    motor2.brake();
  } else {
    motor1.drive(leftMotor);
    motor2.drive(rightMotor);
  }
}

void onEvent(AsyncWebSocket *server, AsyncWebSocketClient *client, AwsEventType type, void *arg, uint8_t *data, size_t len) {
  switch (type) {
    case WS_EVT_CONNECT:
      Serial.printf("WebSocket client #%u connected from %s\n", client->id(), client->remoteIP().toString().c_str());
      break;
    case WS_EVT_DISCONNECT:
      Serial.printf("WebSocket client #%u disconnected\n", client->id());
      break;
    case WS_EVT_DATA:
      handleWebSocketMessage(arg, data, len);
      break;
    case WS_EVT_PONG:
    case WS_EVT_ERROR:
      break;
  }
}

void initWebSocket() {
  ws.onEvent(onEvent);
  server.addHandler(&ws);
}

void setup()
{
  Serial.begin(115200);
  pinMode(RELAY_PIN, OUTPUT);  
  pinMode(LED_PIN, OUTPUT);

  initWiFi();
  initWebSocket();
  server.on("/", HTTP_GET, [](AsyncWebServerRequest *request) {
    request->send_P(200, "text/html", index_html);
  });
  server.begin();
}

void loop()
{
  ws.cleanupClients();

  digitalWrite(RELAY_PIN, fire);
  digitalWrite(LED_PIN, led);

  // Failsafe: If connection drops while joystick is virtually "pushed", stop motors
  if ((joyX != 0 || joyY != 0) && (millis() - lastCommandTime > COMMAND_TIMEOUT)) {
    Serial.println("Command timeout! Stopping motors.");
    motor1.brake();
    motor2.brake();
    joyX = 0;
    joyY = 0;
  }
}

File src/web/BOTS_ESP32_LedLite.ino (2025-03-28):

#include <TB6612_ESP32.h>
#include <WiFi.h>
#include <AsyncTCP.h>
#include <ESPAsyncWebServer.h>
#include <Arduino_JSON.h>
#include <LiteLED.h> // v1.2.1 is compitable with ESP32 v2.0.15 used for BOTS; DOCS: https://github.com/Xylopyrographer/LiteLED

#define LED_TYPE        LED_STRIP_WS2812
#define LED_TYPE_IS_RGBW 0

#define LED_GPIO 16
#define LED_BRIGHT 50
static const crgb_t L_BLUE = 0x0000ff;
LiteLED myLED( LED_TYPE, LED_TYPE_IS_RGBW ); 

#define AIN1 13 // ESP32 Pin D13 to TB6612FNG Pin AIN1
#define BIN1 12 // ESP32 Pin D12 to TB6612FNG Pin BIN1
#define AIN2 14 // ESP32 Pin D14 to TB6612FNG Pin AIN2
#define BIN2 27 // ESP32 Pin D27 to TB6612FNG Pin BIN2
#define PWMA 26 // ESP32 Pin D26 to TB6612FNG Pin PWMA
#define PWMB 25 // ESP32 Pin D25 to TB6612FNG Pin PWMB
#define STBY 33 // ESP32 Pin D33 to TB6612FNG Pin STBY

const char* ssid = "bots2024";
const char* password = "bots12345";

#define RELAY_PIN 15 // pin G15

int speed = 255;
int direction = 0;
int slider = 0;
int fire = 0;
int led = 0;

AsyncWebServer server(80);
AsyncWebSocket ws("/ws");

JSONVar readings;

// these constants are used to allow you to make your motor configuration
// line up with function names like forward.  Value can be 1 or -1
const int offsetA = 1;
const int offsetB = 1;

Motor motor1 = Motor(AIN1, AIN2, PWMA, offsetA, STBY, 5000, 8, 1);
Motor motor2 = Motor(BIN1, BIN2, PWMB, offsetB, STBY, 5000, 8, 2);

const char index_html[] PROGMEM = R"rawliteral(
<!DOCTYPE HTML><html>
<meta name="viewport" content="width=device-width, initial-scale=1.0">

<style>
    body {height: 100vh;overflow: hidden;margin: 0;}
    .parent {
        display: grid;
        grid-template-columns: repeat(2, 1fr);
        grid-template-rows: repeat(2, 1fr);
        grid-column-gap: 0px;
        grid-row-gap: 0px;
        height: 100%;
        }
        
        .div1 { grid-area: 1 / 2 / 3 / 3; height: 100vh;}
        .div2 { grid-area: 1 / 1 / 2 / 2; padding: 0.5rem;}
        .div3 { grid-area: 2 / 1 / 3 / 2; }
        .parent-j {
        display: grid;
        grid-template-columns: repeat(3, 1fr);
        grid-template-rows: repeat(3, 1fr);
        grid-column-gap: 0px;
        grid-row-gap: 0px;
        height: 100%;
        /* justify-items: center;
        align-items: center; */
        }

        .div-u { grid-area: 1 / 2 / 2 / 3; border: 1px solid gray;padding:2rem 3rem; border-radius:100% 100% 0 0;/**display:flex;flex-wrap:nowrap;justify-content:center;align-items:center;**/}
        .div-l { grid-area: 2 / 1 / 3 / 2; border: 1px solid gray;padding:2.95rem 2.4rem; border-radius:100% 0 0 100%;}
        .div-d { grid-area: 3 / 2 / 4 / 3; border: 1px solid gray;padding:2rem 3rem; border-radius:0 0 100% 100%;}
        .div-r { grid-area: 2 / 3 / 3 / 4; border: 1px solid gray;padding:2.95rem 2.4rem; border-radius:0 100% 100% 0;}
        .div-s { grid-area: 2 / 2 / 3 / 3; border: 1px solid rgb(233, 80, 80);padding:3rem 2.3rem; }

        .analog {border:1px solid rgb(216, 211, 211);display: flex;border-radius:15px;justify-content: space-between;align-items: stretch;}
        .analog-value{font-size:5rem;}
        .btn-set{width: 35%;border-radius:0 10px 10px 0;border:none;background:#524FF0;color:white;font-size:1.3rem}
        .analog-data{display: flex;flex-wrap: wrap;align-content: stretch;justify-content: flex-start;padding: 0.5rem;}
        .div-slider{width:100%;}
        .slider{width: 90%;}
        .circ-btn{border-radius:100%;border:1px solid red;width:180px;height:180px;background:none;}
        @media screen and (orientation: portrait) {
            .parent {
                display: grid;
                grid-template-columns: 1fr;
                grid-template-rows: repeat(3, 1fr);
                grid-column-gap: 0px;
                grid-row-gap: 0px;
                }

                .div1 { grid-area: 3 / 1 / 4 / 2; height: auto;}
                .div2 { grid-area: 2 / 1 / 3 / 2; }
                .div3 { grid-area: 1 / 1 / 2 / 2; }
        }
</style>
<div class="parent">
    <div class="div1">
        <div class="parent-j">
            <button class="div-u" id="btn-up">F</button>
            <button class="div-l" id="btn-lt">L</button>
            <button class="div-d" id="btn-dn">B</button>
            <button class="div-r" id="btn-rt">R</button>
            <button class="div-s" id="btn-sp">STOP</button>
        </div>
    </div>
    <div class="div2">
        <div class="analog">
            <div class="analog-data"><div class="analog-value" id="slider-txt">0</div>
                <div class="div-slider"><input id="slider-val" class="slider" type="range" value="0" min="0" max="255"/></div>
            </div> 
            <button class="btn-set" id="btn-set">SET</button>
        </div>
    </div>
    <div class="div3"><button class="circ-btn" id="btn-fire">RELAY</button><button class="circ-btn" id="btn-led">LED</button></div>
</div>

<script>
let gateway = `ws://${window.location.hostname}/ws`;

let sliderTxt = document.querySelector("#slider-txt");
let sliderVal = document.querySelector("#slider-val");
let fireBtn = document.querySelector("#btn-fire");
let ledBtn = document.querySelector("#btn-led");
let ledState = 0;
let fireState = 0;

let websocket;
window.addEventListener('load', onload);

function onload(event) {
    initWebSocket();
    initButtons();
}
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

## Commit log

2022-12-12 basic setup
    [Belt.stl, Leg_holder.stl, Legs.stl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]
2022-12-15 geared wheel add
    [wheel_geared.stl]
2022-12-15 upd to legs
    [Legs_v2.stl]
2022-12-15 fix wheels for belt
2022-12-15 wrong legs
    [Legs_v2.stl]
2022-12-15 wrong lesgs too
    [Legs.stl]
2022-12-15 some new legs
    [Legs_v2.stl]
2022-12-19 extended platform
    [platform.dwg]
2022-12-19 wider holes
2022-12-19 sensor holder add
    [SensorHolder.stl]
2022-12-19 patch add
    [platform_patch.dwg]
2023-01-10 upd to belt
2023-03-01 test shft Creality FFF v0.1
    [MotorHolders.stl, TestShaft_v01.stl]
2023-03-01 dxf add
    [ShaftProfile.dxf]
2023-11-05 add rhino
    [platform_patch_v2.dxf, platform_v2.dxf]
2023-11-07 fix holes
    [platform_v2.dxf]
2023-11-07 add switch holder
    [switchHolder.stl]
2023-11-07 add pen holder
    [penHolder.stl]
2023-11-07 add new platform v3
    [platform_w_penholder_v3.dxf]
2023-11-09 fix holes issue
    [platform_w_penholder_v3.dxf]
2023-11-10 laser cut pen holder
    [penHolder.dxf]
2024-03-11 add gerber
2024-03-16 add Modela compatible files
    [esp8266tb6612_reflected_fixedPitch.dxf]
2024-03-27 fix skipped gnd
    [esp8266tb6612_reflected_fixedPitch.dxf]
2024-03-27 add encoder pins
    [esp8266tb6612_reflected_encoder.dxf]
2024-04-21 add encoder dc control code
2024-04-27 add actual pid
2024-05-02 fix common power
    [ESP8266TB6612_ENC_SeparatedPower.dxf]
2024-05-02 add silk layer
    [ESP8266TB6612_ENC_SeparatedPower_silk.dxf]
2024-05-04 fix vectors
    [ESP8266TB6612_ENC_SeparatedPower_silk.dxf]
2024-05-07 add pscb for 4 motors control
    [ESP322_TB6612x2_DoubleSided.dxf, PCB_Double.3dm]
2024-05-11 add omni coupler
    [Coupler6x8_M4.stl]
2024-05-19 add x4 motors pins test
2024-05-21 fix pins
    [PCB_Double.3dm]
2024-05-23 new v of pcb
    [ESP32_TB6612x2_DoubleSided_v2.dxf, PCB_Double (1).3dm]
2024-05-29 fix isolation
    [ESP32_TB6612x2_DoubleSided_v2.dxf, PCB_Double (1).3dm]
2024-05-31 fix lost holes
    [ESP32_TB6612x2_DoubleSided_v2.dxf, PCB_Double (1).3dm]
2024-06-26 add coupler cad
    [DC_ENC_6to8_coupler.3dm]
2024-07-28 joytick on DOIT ESP32 30 pin
2024-08-08 add cam
    [ESP32_Joystick_Rhino8.3dm]
2024-08-10 fix pcb
    [ESP32_Joystick_Rhino8.3dm]
2024-08-12 add silk
    [SilkBOTS-Shield.dxf]
2024-08-13 KIT CAD
2024-08-14 fix back holes
    [ESP32_Joystick_Rhino8 (1).3dm]
2024-08-15 fix j
    [capJpystick.dxf]
2024-08-16 add clamps
2024-08-16 add STL
    [cap.stl, clamp.stl, level3.stl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]
2024-08-18 fix clamp
2024-08-19 fix clamps
    [shell.stl]
2024-08-21 fix vector
    [cap_aracal.dxf]
2024-09-06 tidy up
    [Belt.stl, Botsx2_Silk.dxf, Coupler6x8_M4.stl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]
2024-09-06 add led mtx
2024-09-15 upd traces outline
2024-09-30 add silk cdr for laser eng
2024-10-01 fix boards link
2024-11-27 early v3
    [ESP32TB6612_MOSFET_vector.dxf]
2024-11-28 add v2 alpha
    [BOTS_PCB_2.0.3dm]
2024-11-29 fix dc-dc
    [BOTS_PCB_2.0.3dm]
2024-12-02 add led
    [BOTS_PCB_2.0.3dm]
2025-01-24 add new servo example
2025-01-24 add big servo
2025-09-18 add e assembly
2025-09-18 add e assembly v1
2025-10-27 add flyback diode
2025-10-28 add schematics
    [BOM_tb6612esp32_2025-10-28.csv]
2026-03-26 fix tb6612 vcc pin
    [BOTS_PCB_2.0_R7.3dm, BOTS_PCB_2.2_TRACES_MIRROR.dxf]
2026-04-09 rotate j1 90 deg
    [Minibot_joystick.3dm]
